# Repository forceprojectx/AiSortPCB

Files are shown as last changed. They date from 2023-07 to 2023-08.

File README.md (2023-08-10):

# AiSort Arduino
This is a PCB for the [AI Case Sorter CS7.1](https://github.com/sjseth/AI-Case-Sorter-CS7.1) project. It feeatures connectors which match the parts list with the exception of the proximity sensor which does not include a connector.

Uses bluetooth for pc connectivity because I am big dumb and forgot that the webcam needs to plug in, so it can't be a fully wireless connection.

## Microcontroller
Uses 3.3V Arduino pro mini as controller 

## Motor Drivers
supports both the TCM 2209 and DRV8825 motor controllers. You can use a matched pair or mix and match, based on what components you have on hand.

## PC Connectivity
The AiSort board is designed to use HC-05 bluetooth modules for PC connectivity. If your PC does not have bluetooth, you may connect a USB-UART device to the pins labeled `TX0` and `RXI`  on the microcontroller or connector J2. 
`TXO` is connected to `J2.1`  
`RXI` is connected to `J2.2`  
`GND` is connected to `J2.8`  
`VCC` is connected to `J2.7`  

## Fan Connectors
Features 3 fan connectors. Two standard 3 pin fan connectors (KF2510-3P) and one 2 pin JST XH type connector. 

## External Trigger Out
The board has two ports to connect external 12volt triggered devices. These are KF2510-2A connectors as found here [KF2510 Connector Kit](https://www.amazon.com/dp/B01M69TKAM)
These triggers can be used to trigger the air solenoid or a round counter or whatever.
> Only one is currently functional due to the limited pinout of the arduino pro mini.

## Proximity Sensor
Unfortunately the proximity sensor does not come with a default connector.
The board is designed to use a JST XH-5A. It is 5 pin only to ensure it does not mate with the other connectors on the board such as the homing sensors. Pin 3 is the signal pin. Power and ground pins are doubled so you can use either of Pins 1 and 2 for ground and either of Pins 4 and 5 for +12v. 
If you have a soldering iron, you can just solder the wires directly to the board if you dont have the appropriate connectors and crimping tools.

## Parts Links
[KF2510 Connector Kit](https://www.amazon.com/dp/B01M69TKAM)

[JST-XH & JST-SM Connector Kit with Crimp Tool](https://www.amazon.com/gp/product/B09X111BK5) (can be used to crimp KF2510 as well)

[Arduino pro mini 3.3V](https://www.ebay.com/itm/404241279783)

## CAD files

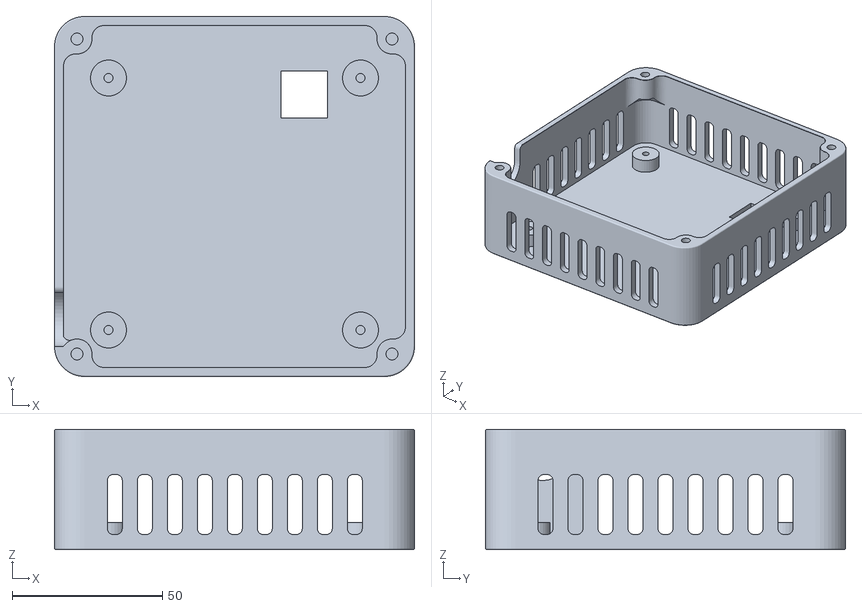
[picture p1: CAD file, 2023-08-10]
Ai Sort Enclosure.stl
120.0 x 120.0 x 40.0

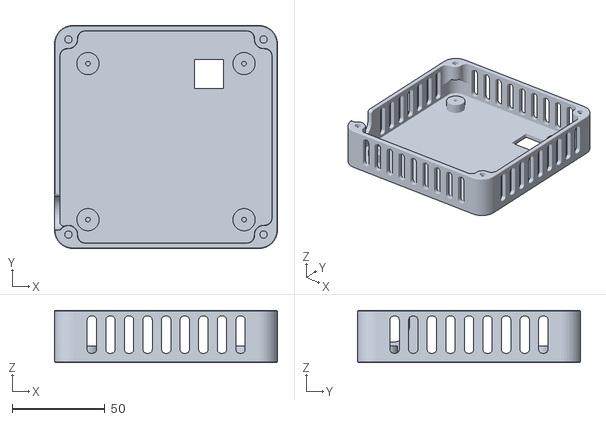
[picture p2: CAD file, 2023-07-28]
AiSort Enclosure -- Low Profile.stl
120.0 x 120.0 x 28.0

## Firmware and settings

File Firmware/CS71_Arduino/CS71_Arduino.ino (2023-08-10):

/// VERSION CS 7.1.230725.1 ///
/// REQUIRES AI SORTER SOFTWARE VERSION 1.1.0 or newer

#include <Wire.h>
#include <SoftwareSerial.h>

//PIN CONFIGURATIONS
//ARDUINO UNO WITH 4 MOTOR CONTROLLER
//Stepper controller is set to 16 Microsteps (3 jumpers in place)

#define FEED_DIRPIN 5 //maps to the DIRECTION signal for the feed motor
#define FEED_STEPPIN 2 //maps to the PULSE signal for the feed motor
#define FEED_Enable 8 //maps to the enable pin for the FEED MOTOR (on r3 shield enable is shared by motors)
#define FEED_MICROSTEPS 16  //how many microsteps the controller is configured for. 
#define FEED_HOMING_SENSOR 13  //connects to the feed wheel homing sensor
#define FEED_SENSOR 9 //the proximity sensor under the feed wheel 
#define FEEDSENSOR_ENABLED true //enabled if feedsensor is installed and working;//this is a proximity sensor under the feed tube which tells us a case has dropped completely
#define FEEDSENSOR_TYPE 0 // NPN = 0, PNP = 1
#define FEED_DONE_SIGNAL 12   // Writes HIGH Signal When Feed is done. Used for mods like AirDrop
#define FEED_HOMING_ENABLED true //enabled feed homing sensor
// Micro-step settings
#define FEED_MSTEP_1 A3
#define FEED_MSTEP_2 A2
#define FEED_MSTEP_3 A7

#define SORT_DIRPIN 6 //maps to the DIRECTION signal for the sorter motor
#define SORT_STEPPIN 3 //maps to the PULSE signal for the sorter motor
#define SORT_Enable 8 //maps to the enable pin for the FEED MOTOR (on r3 shield enable is shared by motors)
#define SORT_MICROSTEPS 16 //how many microsteps the controller is configured for. 
#define SORT_HOMING_SENSOR 11  //connects to the sorter homing sensor
// Micro-step settings
#define SORT_MSTEP_1 A1
#define SORT_MSTEP_2 A0
#define SORT_MSTEP_3 A6

#define CAMERA_LED 10

//ARDUINO CONFIGURATIONS

// Configures the DIR pin on the motor controllers so that the motors turn the way the code expects
#define FEED_DIR_FORWARD HIGH
#define SORT_DIR_FORWARD LOW
#define SORT_DIR_BACKWARD HIGH

//number of steps between chutes. With the 8 and 10 slot attachments, 20 is the default. 
//If you have customized sorter output drops, you will need to change this setting to meet your needs. 
//Note there are 200 steps in 1 revolution of the sorter motor. 
#define SORTER_CHUTE_SEPERATION 20 


#define FEED_HOMING_OFFSET_STEPS 3 //additional steps to continue after homing sensor triggered
#define FEED_STEPS 70  //The amount to travel before starting the homing cycle. Should be less than (80 - FEED_HOMING_OFFSET_STEPS)
#define FEED_OVERSTEP_THRESHOLD 90 //if we have gone this many steps without hitting a homing node, something is wrong. Throw an overstep error

//FEED MOTOR ACCELLERATION SETTINGS (DISABLED BY DEFAULT)
#define FEED_ACC_SLOPE 32  //2 steps * 16 MicroStes

#define FEED_MOTOR_SPEED 94 //range of 1-100
#define ACC_FEED_ENABLED false //enabled or disables feed motor accelleration. 

//SORT MOTOR ACCELLERATION SETTINGS (ENABLED BY DEFAULT)
#define ACC_SORT_ENABLED true
#define SORT_MOTOR_SPEED 94 //range of 1-100
#define SORT_ACC_SLOPE 64 //this is the number of microsteps to accelerate and deaccellerate in a sort. 
#define ACC_FACTOR 1200
#define SORT_HOMING_ENABLED true
//FEED DELAY SETTINGS

// Used to send signal to add-ons when feed cycle completes (used by airdrop mod). 
// IF NOT USING MODS, SET TO 0. With Airdrop set to 60-100 (length of the airblast)
#define FEED_CYCLE_COMPLETE_SIGNALTIME 30 

// The amount of time to wait after the feed completes before sending the FEED_CYCLE_COMPLETE SIGNAL
// IF NOT USING MODS, SET TO 0. with Airdrop set to 30-50 which allows the brass to start falling before sending the blast of air. 
#define FEED_CYCLE_COMPLETE_PRESIGNALDELAY 0

// Time in milliseconds to wait before sending "done" response to serialport (allows for everything to stop moving before taking the picture): runs after the feed_cycle_complete signal
// With AirDrop mod enabled, it needs about 20-30MS. If airdrop is not enabled, it should be closer to 50-70. 
// If you are getting blurred pictures, increase this value. 
#define FEED_CYCLE_NOTIFICATION_DELAY 80 

// number of MS to wait after feedcycle before moving sort arm.
// Prevents slinging brass. With AirDrop Mod enabled, this can be 100 or lower, if not enabled, set to 400 or more. 
// This gives time for the brass to clear the sort tube before moving the sort arm. 
#define SLOT_DROP_DELAY 300


///END OF USER CONFIGURATIONS ///
///DO NOT EDIT BELOW THIS LINE ///


int feedSpeed = FEED_MOTOR_SPEED; //represents a number between 1-100
int feedSteps = FEED_STEPS;
int feedMotorSpeed = 500;//this is default and calculated at runtime. do not change this value

int sortSpeed = SORT_MOTOR_SPEED; //represents a number between 1-100
int sortSteps = SORTER_CHUTE_SEPERATION;
int sortMotorSpeed = 500;//this is default and calculated at runtime. do not change this value
int homingSteps = 0;

int feedMicroSteps = feedSteps * FEED_MICROSTEPS;

const int feedramp = (ACC_FACTOR + (FEED_MOTOR_SPEED /2)) / FEED_ACC_SLOPE;
const int sortramp = (ACC_FACTOR + (SORT_MOTOR_SPEED /2)) / SORT_ACC_SLOPE;
const int feedOverTravelSteps = feedMicroSteps - (FEED_OVERSTEP_THRESHOLD * FEED_MICROSTEPS);
const int feedHomingOffset = FEED_HOMING_OFFSET_STEPS * FEED_MICROSTEPS;

bool FeedScheduled = false;
bool IsFeeding = false;
bool IsFeedHoming = false;
bool IsFeedHomingOffset = false;
bool FeedCycleInProgress = false;
bool FeedCycleComplete = false;
bool IsFeedError = false;

int FeedSteps = feedMicroSteps;
int FeedHomingOffsetSteps = feedHomingOffset;
int feedDelayMS = 150;
int sortDelayMS = 400;

bool forceFeed=false;
String input = "";
int qPos1 = 0;
int qPos2 = 0;
int sortStepsToNextPosition = 0;
int sortStepsToNextPositionTracker=0;
bool SortInProgress = false;
bool SortComplete = false;
bool IsSorting = false;
bool IsSortHoming = false;
int slotDelayCalc = 0;

bool IsTestCycle=false;
bool IsSortTestCycle=false;
int testCycleInterval=0;
int testsCompleted=0;
int sortToSlot=0;
unsigned long theTime;
unsigned long timeSinceLastSortMove;
unsigned long msgResetTimer;

uint8_t LedPwmValue;


void setup() {
  Serial.begin(9600);
  Serial.print("Ready\n");
  
  setSorterMotorSpeed(SORT_MOTOR_SPEED);
  setFeedMotorSpeed(FEED_MOTOR_SPEED);

  pinMode(FEED_Enable, OUTPUT);
  pinMode(SORT_Enable, OUTPUT);
  pinMode(FEED_DIRPIN, OUTPUT);
  pinMode(FEED_STEPPIN, OUTPUT);
  pinMode(SORT_DIRPIN, OUTPUT);
  pinMode(SORT_STEPPIN, OUTPUT);

  pinMode(CAMERA_LED, OUTPUT);

  pinMode(FEED_DONE_SIGNAL, OUTPUT);
  pinMode(FEED_HOMING_SENSOR, INPUT);
  pinMode(SORT_HOMING_SENSOR, INPUT);
  pinMode(FEED_SENSOR, INPUT);

  pinMode(SORT_MSTEP_1, OUTPUT);
  pinMode(SORT_MSTEP_2, OUTPUT);
  pinMode(SORT_MSTEP_3, OUTPUT);
  pinMode(FEED_MSTEP_1, OUTPUT);
  pinMode(FEED_MSTEP_2, OUTPUT);
  pinMode(FEED_MSTEP_3, OUTPUT);

  /*
    TCM2209 Micro step config
    MS2   MS1   Micro Steps
     0     0    8
     0     1    2 (half step)
     1     0    4 (quarter step)
     1     1    16
  */
  digitalWrite(SORT_MSTEP_1, HIGH);
  digitalWrite(SORT_MSTEP_2, HIGH);
  digitalWrite(SORT_MSTEP_3, LOW);
  digitalWrite(FEED_MSTEP_1, HIGH);
  digitalWrite(FEED_MSTEP_2, HIGH);
  digitalWrite(FEED_MSTEP_3, LOW);


  digitalWrite(FEED_Enable, LOW);
  digitalWrite(SORT_Enable, LOW);
  digitalWrite(FEED_DIRPIN, FEED_DIR_FORWARD);

  LedPwmValue=127;
  analogWrite(CAMERA_LED, LedPwmValue);

  IsFeedHoming=true;
  IsSortHoming=true;
  msgResetTimer = millis();
}


void loop() {
   checkSerial();
   runSortMotor();
   onSortComplete();
   scheduleRun();
   checkFeedErrors();
   runFeedMotor();
   homeFeedMotor();
   homeSortMotor();
   serialMessenger();
   onFeedComplete();
   runAux();
}

bool commandReady = false;
char endMarker = '\n';
char rc;

void recvWithEndMarker() {
    while (Serial.available() > 0 ) {
        rc = Serial.read();
        delay(1);
        if (rc != endMarker) {
            input += rc;
        }
        else {
            commandReady=true; 
            return;
        }
    }
 }
void resetCommand(){
  input="";
  commandReady=false;
}

void checkSerial(){
  if(FeedCycleInProgress==false && SortInProgress==false && Serial.available()>0){
      //input = Serial.readStringUntil('\n');
       recvWithEndMarker();
       
       if(!commandReady){
        return;
       }
      // Serial.print(input);
       
     //this should be most cases
      if (isDigit(input[0])) {
        moveSorterToNextPosition(input.toInt());
        FeedScheduled = true;
        IsFeeding = false;
        scheduleRun();
        resetCommand();
        return;
      }
      if (input.startsWith("homefeeder")) {
        feedDelayMS=400;
          IsFeedHoming=true;
         Serial.print("ok\n");
         resetCommand();
         return;
      } 
      if (input.startsWith("homesorter")) {
        sortDelayMS=400;
          IsSortHoming=true;
          Serial.print("ok\n");
          resetCommand();
         return;
      } 
      if (input.startsWith("stop")) {
      resetCommand();
          FeedScheduled=false;
          IsFeedHoming=false;
          IsFeedHomingOffset = false;
          FeedCycleComplete=true;
          FeedCycleInProgress = false;
         // Serial.print("ok\n");
         return;
      } 

      if (input.startsWith("sortto:")) {
          input.replace("sortto:", "");
          moveSorterToPosition(input.toInt());
           Serial.print("ok\n");
           resetCommand();
         return;
      } 

      if (input.startsWith("xf:")) {
          input.replace("xf:", "");
          forceFeed = true;
          moveSorterToNextPosition(input.toInt());
          resetCommand();
          FeedScheduled = true;
          IsFeeding = false;
          scheduleRun();
          return;
      }

      if (input.startsWith("getconfig")) {
     
        Serial.print("{\"FeedMotorSpeed\":");
        Serial.print(feedSpeed);

        Serial.print(",\"FeedCycleSteps\":");
        Serial.print(feedSteps);

        Serial.print(",\"SortMotorSpeed\":");
        Serial.print(sortSpeed);

        Serial.print(",\"SortSteps\":");
        Serial.print(sortSteps);

        Serial.print("}\n");
        resetCommand();
        return;      
      }

       //set feed speed. Values 1-100. Def 60
      if (input.startsWith("feedspeed:")) {
        input.replace("feedspeed:", "");
        feedSpeed = input.toInt();
        setFeedMotorSpeed(feedSpeed);
        Serial.print("ok\n");
        resetCommand();
        return;
      }

       if (input.startsWith("sortspeed:")) {
        input.replace("sortspeed:", "");
        sortSpeed = input.toInt();
        setSorterMotorSpeed(sortSpeed);
        Serial.print("ok\n");
        resetCommand();
        return;
      }

      //set sort steps. Values 1-100. Def 20
      if (input.startsWith("sortsteps:")) {
        input.replace("sortsteps:", "");
        sortSteps = input.toInt();
        Serial.print("ok\n");
        resetCommand();
        return;
      }

      //set feed steps. Values 1-1000. Def 100
      if (input.startsWith("feedsteps:")) {
        input.replace("feedsteps:", "");
        feedSteps = input.toInt();
        feedMicroSteps = feedSteps * FEED_MICROSTEPS;
        Serial.print("ok\n");
        resetCommand();
        return;
      }
      if (input.startsWith("SetLedIntensity:")) 
      {
        input.replace("SetLedIntensity:", "");
        LedPwmValue = input.toInt();
        analogWrite(CAMERA_LED, LedPwmValue);
         Serial.print("LED Intensity Set\n");
         resetCommand();
         return;
      }

      if (input.startsWith("test:")) {
        input.replace("test:", "");
        IsTestCycle=true;
        testCycleInterval=input.toInt();
        testsCompleted=0;
        FeedScheduled=false;
        FeedCycleInProgress=false;
        Serial.print("testing started\n");
        resetCommand();
        return;
      }

       if (input.startsWith("sorttest:")) {
        input.replace("sorttest:", "");
        IsSortTestCycle=true;
        testCycleInterval=input.toInt();
        testsCompleted=0;
        Serial.print("testing started\n");
        resetCommand();
        return;
      }
      resetCommand();
      Serial.print("ok\n");
  }
}


//this method is to run all "other" routines not in the main duty cycles (such as tests)
void runAux(){

  //This runs the feed and sort test if scheduled
  if(IsTestCycle==true&&FeedScheduled==false&&FeedCycleInProgress==false){
    if(testsCompleted<testCycleInterval){
       int slot = random(1,8);
         moveSorterToNextPosition(slot);
        
        FeedScheduled = true;
        IsFeeding = false;
        scheduleRun();
        
        Serial.print(testsCompleted);
        Serial.print(" - ");
        Serial.print(slot);
        Serial.print("\n");
        testsCompleted++;

            
    }else{
      IsTestCycle=false;
      testCycleInterval=0;
      testsCompleted=0;
    }
  }

  //this runs the sorter only test cycles if scheduled
  if(IsSortTestCycle==true&&SortInProgress==false){
    if(testsCompleted<testCycleInterval){
       int slot = random(0,8);
       delay(40);
       Serial.print(testsCompleted);
       Serial.print(" - Sorting to: ");
       Serial.println(slot);
       moveSorterToPosition(slot);
        testsCompleted++;
    }else{
      moveSorterToPosition(0);
      Serial.println("Sort Test Completed");
      IsSortTestCycle=false;
      testsCompleted=0;
      testCycleInterval=0;
    }
  }
}


void moveSorterToNextPosition(int position){
    sortToSlot=position;
    sortStepsToNextPosition = (qPos1 * sortSteps * SORT_MICROSTEPS) - (qPos2 * sortSteps * SORT_MICROSTEPS);
    sortStepsToNextPositionTracker = sortStepsToNextPosition;
    if(sortStepsToNextPosition !=0){
      theTime = millis();
       slotDelayCalc = (SLOT_DROP_DELAY - (theTime - timeSinceLastSortMove));
       slotDelayCalc = slotDelayCalc > 0? slotDelayCalc : 1;
       //Serial.println(slotDelayCalc);
      delay(slotDelayCalc);
    }
    qPos1 = qPos2;
    qPos2 =position;
    SortInProgress = true;
    SortComplete = false;
    IsSorting = true;
}

void moveSorterToPosition(int position){
    sortToSlot=position;
    sortStepsToNextPosition = (qPos1 * sortSteps * SORT_MICROSTEPS) - (position * sortSteps * SORT_MICROSTEPS);
    sortStepsToNextPositionTracker = sortStepsToNextPosition;
   
  // Serial.println(position);
   //Serial.println(sortStepsToNextPosition);
    qPos1 =position;
    qPos2 =position;
    SortInProgress = true;
    SortComplete = false;
    IsSorting = true;
}

void runSortMotor(){
  if(IsSorting==true){
    
    if(sortStepsToNextPosition==0){
     
      if(qPos1==0){
        homingSteps=0;
         IsSortHoming=true;
      }else{
         IsSorting=false;
         SortComplete = true;
      }
      return;
    }
    setAccSortDelay();
    
    if(sortStepsToNextPosition > 0){
      stepSortMotor(true);
      sortStepsToNextPosition--;
    }
    else {
      stepSortMotor(false);
      sortStepsToNextPosition++;
    }
  }
}
void setAccSortDelay(){
    if(ACC_SORT_ENABLED == false){
      sortDelayMS=sortMotorSpeed;
      return;
    }
    //up ramp
    if((abs(sortStepsToNextPositionTracker) - abs(sortStepsToNextPosition)) < SORT_ACC_SLOPE ){
      sortDelayMS = ACC_FACTOR - ((abs(sortStepsToNextPositionTracker) - abs(sortStepsToNextPosition)) * sortramp);
      if (sortDelayMS < sortMotorSpeed) {
         sortDelayMS = sortMotorSpeed;
      }
     
      return;
    }
  
    //down ramp
    if (abs(sortStepsToNextPositionTracker) - abs(sortStepsToNextPosition) > (abs(sortStepsToNextPositionTracker) - SORT_ACC_SLOPE)){
        sortDelayMS = (SORT_ACC_SLOPE - abs(sortStepsToNextPosition)) * sortramp;
         if (sortDelayMS < sortMotorSpeed) {
             sortDelayMS = sortMotorSpeed;
         }
         if (sortDelayMS > ACC_FACTOR) {
             sortDelayMS = ACC_FACTOR;
         }
         
    }else{
      //normal run speed
      sortDelayMS = sortMotorSpeed;
    }
    
}
void stepSortMotor(bool forward)
{
  if(forward==true)
  {
    digitalWrite(SORT_DIRPIN, SORT_DIR_FORWARD);
  }
  else
  {
    digitalWrite(SORT_DIRPIN, SORT_DIR_BACKWARD);
  }
  digitalWrite(SORT_STEPPIN, HIGH);
  delayMicroseconds(1);  //pulse width
  digitalWrite(SORT_STEPPIN, LOW);
  delayMicroseconds(sortDelayMS); //controls motor speed
}
void onSortComplete(){
  if(SortInProgress==true && SortComplete==true){
        SortInProgress=false;
        timeSinceLastSortMove = millis();
       // Serial.println("runscheduled");
  }
}

void checkFeedErrors(){
 if(FeedCycleComplete == false && FeedSteps < feedOverTravelSteps){
      FeedScheduled=false;
      FeedCycleComplete=true;
      IsFeeding=false;
      IsFeedHoming= false;
      IsFeedHomingOffset=false;
      IsFeedError = true;
      FeedCycleInProgress = false;
      Serial.println("error:feed overtravel detected");
 }
}
void serialMessenger(){
  
 return; 

}

void onFeedComplete(){
  if(FeedCycleComplete==true&& IsFeedError==false){
   
    
    delay(FEED_CYCLE_COMPLETE_PRESIGNALDELAY); //this allows some time for the brass to start dropping before generating the airblast
    digitalWrite(FEED_DONE_SIGNAL, HIGH);
    delay(FEED_CYCLE_COMPLETE_SIGNALTIME);
    digitalWrite(FEED_DONE_SIGNAL,LOW);
    delay(FEED_CYCLE_NOTIFICATION_DELAY);
    Serial.print("done\n");
    //Serial.flush();
    FeedCycleComplete=false;
     forceFeed= false;
    return;
  }
  
}

void scheduleRun(){
 
  if(FeedScheduled==true && IsFeeding==false){
    if(digitalRead(FEED_SENSOR) == FEEDSENSOR_TYPE || forceFeed==true || FEEDSENSOR_ENABLED==false){
      //set run variables
      IsFeedError=false;
      FeedSteps = feedMicroSteps;
      FeedScheduled=false;
      FeedCycleInProgress = true;
      FeedCycleComplete=false;
      IsFeeding=true;
    }else{
      theTime = millis();
      if(theTime - msgResetTimer > 1000){
         // Serial.flush();
          Serial.println("waiting for brass");
         
          msgResetTimer = millis();
      }
    // Serial.flush();
     
    }
  }
}
void runFeedMotor() {
  if(SortInProgress){
    return;
  }
  
  if(IsFeeding==true && FeedSteps > 0 )
  {
    setAccFeedDelay();
    stepFeedMotor();
    FeedSteps--;
    return;
  }
  if(IsFeeding==true){
    IsFeeding=false;
    IsFeedHoming = true;
  }
  return;

}

void homeFeedMotor(){
  
  if(IsFeedHoming==true ){
   
    if(FEED_HOMING_ENABLED == false){
      IsFeedHoming=false;
       IsFeedHomingOffset = false;
      FeedCycleComplete=true;
      FeedCycleInProgress = false;
      return;
    }
    
    if (digitalRead(FEED_HOMING_SENSOR) == 1) {
      IsFeedHoming=false;
      
     // Serial.println("homed!");
      if(FeedCycleInProgress){ //if we are homing initially, we don't need to apply offsets
          IsFeedHomingOffset = true;
          FeedHomingOffsetSteps = feedHomingOffset;
      }
      return;
    }
    stepFeedMotor();
    FeedSteps--;
    return;
  }

  if(IsFeedHomingOffset == true){
    if(feedHomingOffset == 0)
    {
      IsFeedHomingOffset = false;
      FeedCycleComplete=true;
      FeedCycleInProgress = false;
      return;
    }
    if(IsFeedHomingOffset == true && FeedHomingOffsetSteps > 0){
      stepFeedMotor();
    
     // Serial.println(FeedHomingOffsetSteps);
      FeedHomingOffsetSteps--;
      FeedSteps--;
    }
    else if(IsFeedHomingOffset == true && FeedHomingOffsetSteps<=0){
      IsFeedHomingOffset = false;
      FeedCycleComplete=true;
      FeedCycleInProgress = false;
    }
  }
}

void homeSortMotor(){
  if(IsSortHoming==true && SORT_HOMING_ENABLED == false){
     IsSorting=false;
         SortComplete = true;
         IsSortHoming =false;
         return;
    }
  if(IsSortHoming==true){
     
    if(IsSorting==true)
    {
        //code for running sort
         if(digitalRead(SORT_HOMING_SENSOR)==0){
          if(homingSteps < (200*SORT_MICROSTEPS)){
              stepSortMotor(true);  
              homingSteps++;          
          }
          return;
         }
         IsSorting=false;
         SortComplete = true;
         IsSortHoming =false;
    }
    else
    {
      if(digitalRead(SORT_HOMING_SENSOR)==0)
      {
          if(homingSteps < (200*SORT_MICROSTEPS))
          {
              stepSortMotor(true);  
              homingSteps++;          
          }
      }else{
        IsSortHoming=false;
        // Serial.println("Sort Homed!");
      }
    }
  }
}

void stepFeedMotor(){
    digitalWrite(FEED_STEPPIN, HIGH);
    delayMicroseconds(1);  //pulse width
    digitalWrite(FEED_STEPPIN, LOW);
    delayMicroseconds(feedDelayMS); //controls motor speed
}

void setAccFeedDelay(){
    if(ACC_FEED_ENABLED == false){
      feedDelayMS=feedMotorSpeed;
      return;
    }
    //up ramp
    if((feedMicroSteps - FeedSteps) < FEED_ACC_SLOPE ){
      feedDelayMS = ACC_FACTOR - ((feedMicroSteps - FeedSteps) * feedramp);
      if (feedDelayMS < feedMotorSpeed) {
         feedDelayMS = feedMotorSpeed;
      }
      //Serial.println(msdelay);
      return;
    }
  
    //down ramp
    if (feedMicroSteps - FeedSteps > (feedMicroSteps - FEED_ACC_SLOPE)){
        feedDelayMS = (FEED_ACC_SLOPE - FeedSteps) * feedramp;
         if (feedDelayMS < feedMotorSpeed) {
             feedDelayMS = feedMotorSpeed;
         }
         if (feedDelayMS > ACC_FACTOR) {
             feedDelayMS = ACC_FACTOR;
         }
         //Serial.println(msdelay);
    }else{
      //normal run speed
      feedDelayMS = feedMotorSpeed;
    }
    
}

void setSorterMotorSpeed(int speed) {
  sortMotorSpeed = setSpeedConversion(speed);
}
void setFeedMotorSpeed(int speed) {
  feedMotorSpeed = setSpeedConversion(speed);
}

int setSpeedConversion(int speed) {
  if (speed < 1 || speed > 100) {
    return 500;
  }

  return 1060 - ((int)(((double)(speed - 1) / 99) * (1000 - 60)) + 60);
}

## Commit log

2023-07-28 first commit. Submitted to jlcpcb for fab on july 20, 2023
    [AiSort Enclosure -- Low Profile.stl]
2023-07-28 update PCB to include prox sensor wire colors on the silk screen to aid in connecting the prox sensor.
    add README.md with some minor documentation
2023-07-28 add connector kit links to readme file
2023-07-31 shrink mounting holes to 3.96mm (atx/itx standard)
2023-08-02 Fix various rev1 issues and bump version number
    * add 10k pull down to PROX_SENSOR_3V3 net
    * swap pins for Camera LED and one of the home sensors to allow use of standard arduino PWM on pin 10 to dim the camera.
    * add layer indicators
    * adjust revision text on PCB layout
    * adjust position of component identifiers on silk screen
2023-08-04 swap power and ground pins on the molex connector
2023-08-10 first push
    [Ai Sort Enclosure.stl]
2023-08-17 Implement power LED. Make some minor improvements for manufacturability.
    Single sided load. Bottom layer components have been moved to the top layer.
    Consolidate resistor values. Status LEDs now all use 300 ohm resistors.
